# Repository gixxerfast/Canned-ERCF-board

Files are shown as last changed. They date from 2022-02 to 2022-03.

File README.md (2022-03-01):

# Canned-ERCF-board v1.0-beta2
Enraged Rabbit Carrot Feeder CAN-FD expansion board for Duet3

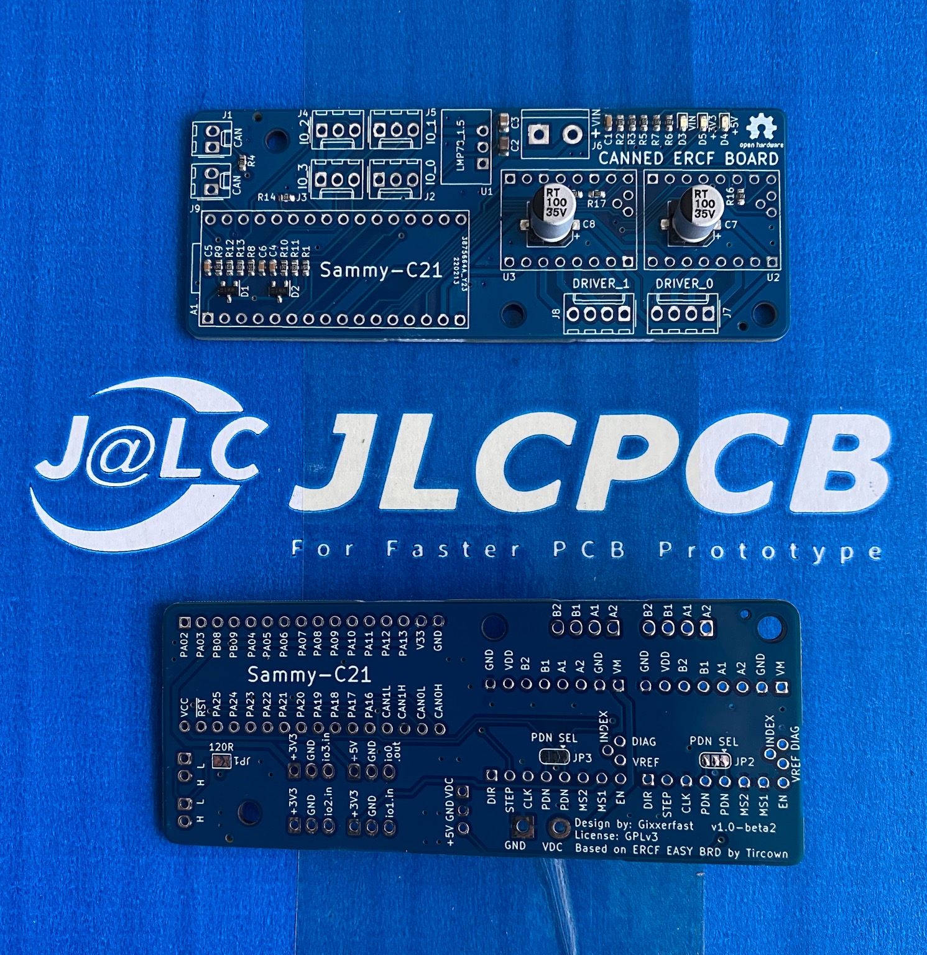
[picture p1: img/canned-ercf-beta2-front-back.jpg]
Canned ERCF boards V1.0-beta2 front and back from JLCPCB


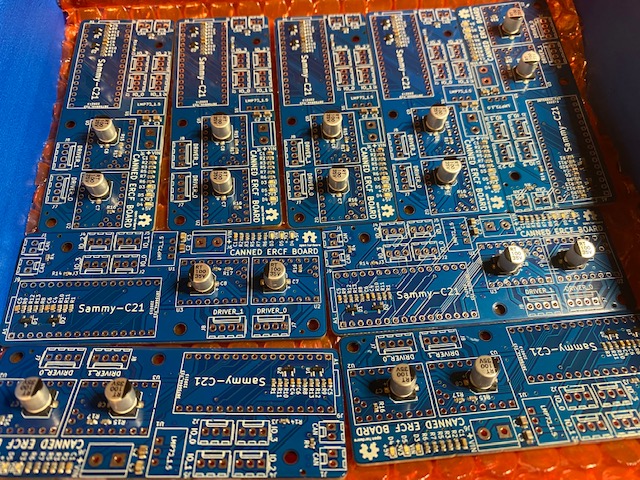
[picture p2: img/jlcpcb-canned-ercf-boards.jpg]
Canned ERCF Boards V1.0-beta2 from JLCPCB


The Canned ERCF board is a general purpose Duet 3 CAN extansion board but specifically made to support the [ERCF](https://github.com/EtteGit/EnragedRabbitProject) multifilament feeder system based on the [ERCF Easy Brd](https://github.com/Tircown/ERCF-easy-brd) by Tircown.

Check out the [Duet RRF ERCF macros](https://github.com/pfn/EnragedRabbitOnRRF?ref=https://coder.social) by pfn. With these macros you should be able to use a RRF equipped printer and run multi filament prints as with the original ERCF macros as long as you have enough ports and motors available.

The board uses a Atmel/Microchip SAM C21 microcontroller module with USB and CAN, the [Sammy-C21](https://www.chip45.com/products/sammy-c21-1.0_atmel_smart_arm_sam_module_samc21_usb_dual_can_duet3d.php) from [Chip45](https://www.chip45.com/).

The firmware is a modified version of the [Duet3Expansion Sammy-C21 firmware](https://github.com/Duet3D/Duet3Expansion) by [Duet3D](https://www.duet3d.com/)  

You can find the fork of the modfied Duet firmware [here](https://github.com/gixxerfast/Duet3Expansion/tree/cannedboard). As the versions are moving rapidly with the new RRF version 3.4 there's no guarantees that this will be kept in synch.

**Please note that this board will not work with the standard Duet Sammy firmware.**

The board features the following functions:

- Support for up to two TMC2209 stepsticks Stepper motor drivers with UART control
- 1500 mA 24V-5V efficient switching voltage regulator. 
- Three GPIO inputs 3.3V signal inputs that may be used for encoders and endstops with 3.3V source.
- One 3.3V PWM output for hobby micro servo control with 5V source. Note that the general advice is not to source power to the servo via the board but to have a separate 5V source.
- MCU Module. It's using the Atmel/Microchip ATSAMC21G18A based Sammy-C21 MCU-module
- Input over voltage protection up to 30V
- VIN voltage monitoring.
- Three led indicators for 3.3V, 5V and VIN (24V). Easy troubleshooting if missing a rail. 

As an extension this board has CAN-FD support and is connected to another Duet 3 board via the CAN bus. Firmware is updated via CAN and the DWC (Duet Web Control frontend) so the USB-port is not really used.

This board can be used with the Sammy-C21 Duet 3 extension board firmware together with my modified configuration file. No further modifications are required (to this date).

There's a 4.7 Kohms pullup resistor on the TX/RX UART line as the BTT TMC2209 stepsticks has a 20K ohms pulldown resistor on the same line. The Duet firmware will disable the UART line before reading and writing causing the the line to go low and therefore corrupt the UART messaging. With the 4.7 Kohms pullup resistor the line is kept high all the time and the communication can function undisturbed.

There are two pin pairs for the CAN bus so either the CAN-bus can be terminated by closing the solder brideg on the back of the board or it can be routed to the next board in the chain,

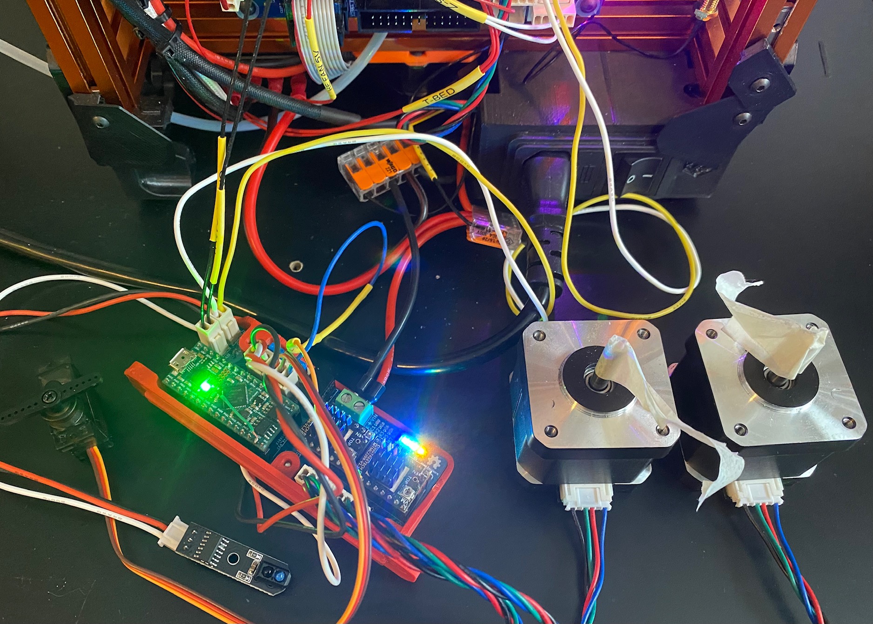
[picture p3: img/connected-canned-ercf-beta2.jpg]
Canned ERCF Board connected to Voron V0.1 Duet 3 mini5+ via CAN


## BOM
Apart from the board as specified in the KiCad files with the SMT components which I have had mounted by JLCPCB, there a number of components needed to complete the board

- 1 x Sammy-C21 ATSAMC21G18A MCU module from [Chip45](https://www.chip45.com/) or [Filastruder](https://www.filastruder.com/products/sammy-c21-v1-0-duet3d-module)
- 2 x BTT TMC2209 stepstick modules
- 1 x LMP78_05-1.5 or compatible DC-DC voltage converter
- 2 x 16 pin PCB connection headers
- 4 x 8 pin PCB connection headers
- 2 x 2 pin PCB connection headers
- 2 x 2 pin MOLEX KK254 (or equivalent) male PCB connectors
- 4 x 3 pin Molex KK254 (or equivalent) male PCB connectors
- 2 x 4 pin Molex KK254 (or equivalent) male PCB connectors
- 1 x 2 pin Phoenix 5.08 Screw connector. Part # 277-1247-ND or eqivalent

### Disclaimer 
This is work in progress and it's right now under development and there may exist issues with this version that may or may not be corrected in the next version. It's based on many parts over which I have no control over at all. I take no responsibilty whatsoever for the functionality or safety and I claim the right to not inform about anything about this product known to me now or in the future. This is soley at your own risk and I accept no responsiblity, financially or otherwise, if it causes your controller board to break, your house to burn down, your wife to divorce you, if it simply doesn't work at all or any other scenario possible in any multiverse. If you do not accept that all responibility for use of this product is your own, please don't download, build or use it.

## License - Open hardware / Open software
This project and its content is realeased under the [GPLv3 license](https://www.gnu.org/licenses/gpl-3.0.html)

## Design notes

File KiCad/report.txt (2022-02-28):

Plotted to 'C:\Users\gixxe\repos\Canned-ERCF-board\KiCad\gerber\canned-ercf-board-F_Cu.gtl'.
Plotted to 'C:\Users\gixxe\repos\Canned-ERCF-board\KiCad\gerber\canned-ercf-board-B_Cu.gbl'.
Plotted to 'C:\Users\gixxe\repos\Canned-ERCF-board\KiCad\gerber\canned-ercf-board-F_Paste.gtp'.
Plotted to 'C:\Users\gixxe\repos\Canned-ERCF-board\KiCad\gerber\canned-ercf-board-F_Silkscreen.gto'.
Plotted to 'C:\Users\gixxe\repos\Canned-ERCF-board\KiCad\gerber\canned-ercf-board-B_Silkscreen.gbo'.
Plotted to 'C:\Users\gixxe\repos\Canned-ERCF-board\KiCad\gerber\canned-ercf-board-F_Mask.gts'.
Plotted to 'C:\Users\gixxe\repos\Canned-ERCF-board\KiCad\gerber\canned-ercf-board-B_Mask.gbs'.
Plotted to 'C:\Users\gixxe\repos\Canned-ERCF-board\KiCad\gerber\canned-ercf-board-Edge_Cuts.gm1'.
Info: Done.

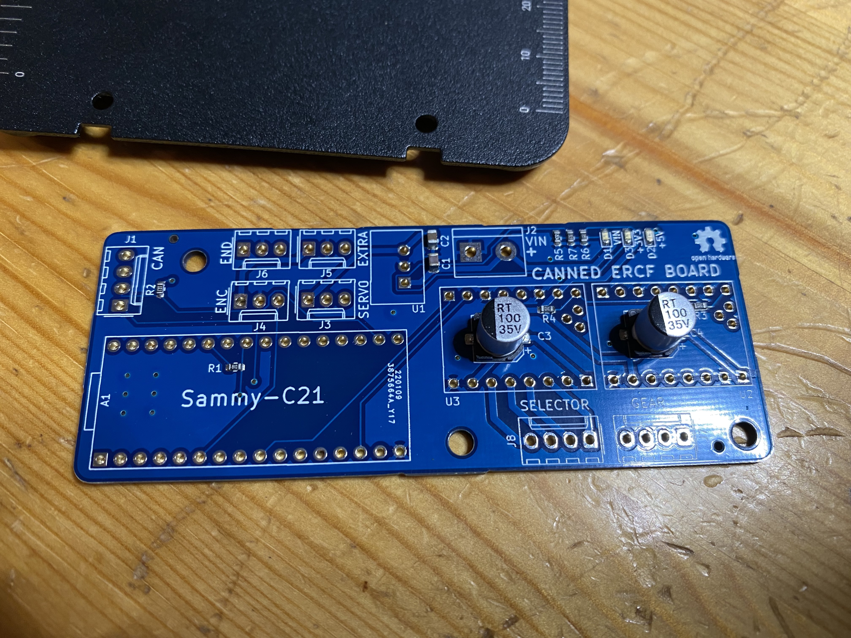
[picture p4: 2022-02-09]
img/canned-ercf-board-front.jpg

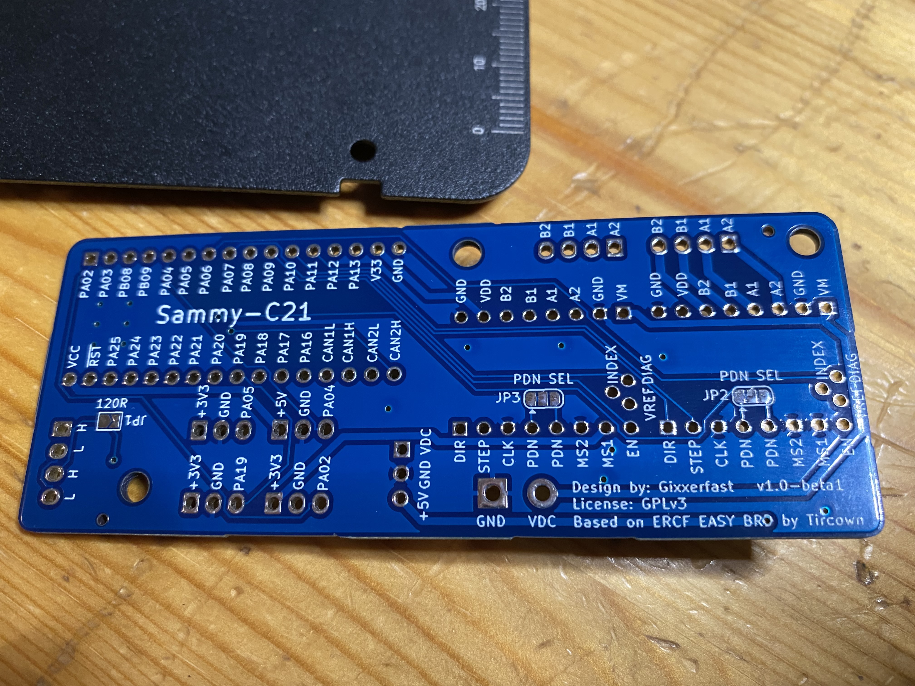
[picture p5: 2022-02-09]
img/canned-ercf-board-rear.jpg

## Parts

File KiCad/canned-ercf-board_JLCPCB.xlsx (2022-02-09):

Comment | Designator | Footprint | JLCPCB Part #（optional）
10uF | C1 | Capacitor_SMD:C_0805_2012Metric |  | C342723
22uF | C2 | Capacitor_SMD:C_0805_2012Metric |  | C338080
100uF | C3, C4 | Capacitor_SMD:CP_Elec_6.3x7.7 |  | C267470
Blue | D1, D2, D3 | LED_SMD:LED_0603_1608Metric |  | C138541
1k | R1, R6 | Resistor_SMD:R_0603_1608Metric |  | C116692
120R | R2 | Resistor_SMD:R_0603_1608Metric |  | C365072
10k | R3, R4 | Resistor_SMD:R_0603_1608Metric |  | C98220
4K7 | R5 | Resistor_SMD:R_0603_1608Metric |  | C99782
470R | R7 | Resistor_SMD:R_0603_1608Metric |  | C114669

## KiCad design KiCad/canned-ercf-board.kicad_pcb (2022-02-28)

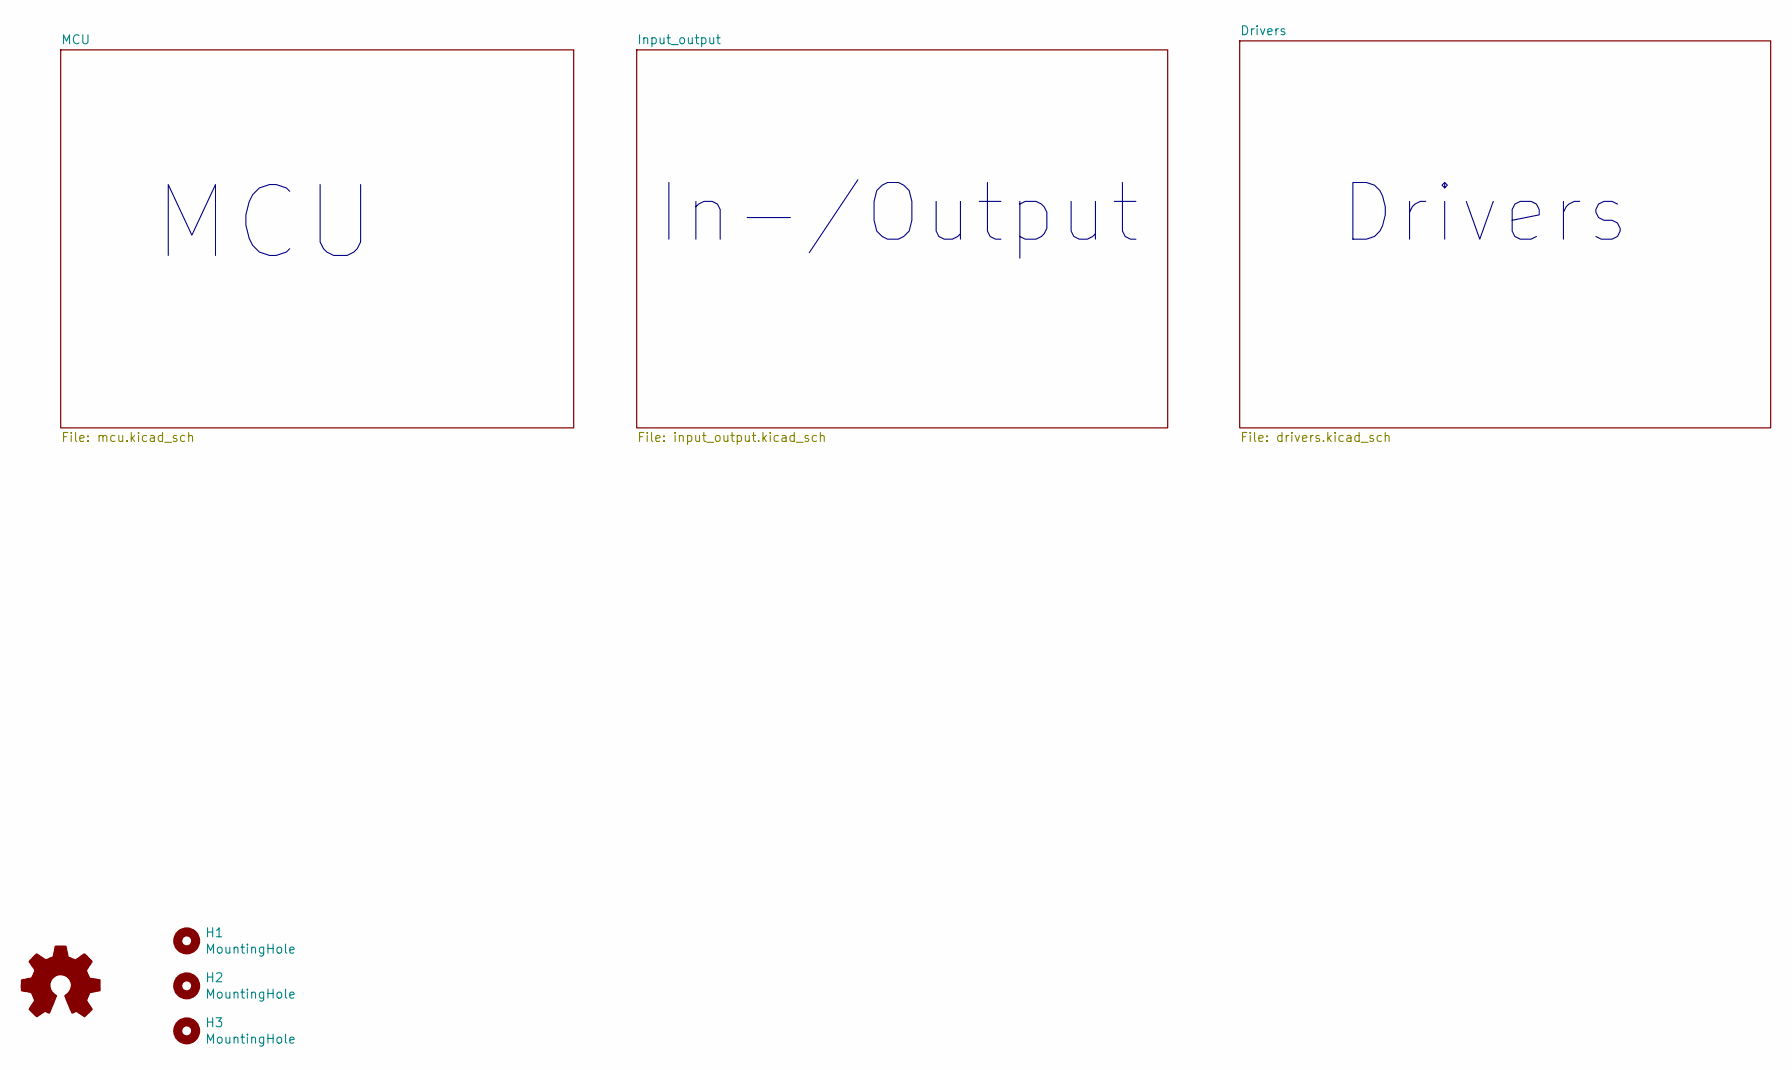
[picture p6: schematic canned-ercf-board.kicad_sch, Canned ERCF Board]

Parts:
H1, H2, H3: MountingHole; MountingHole_3.2mm_M3
L1: Logo_Open_Hardware_Small; OSHW-Logo2_7.3x6mm_SilkScreen

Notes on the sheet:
MCU
Drivers
In-/Output

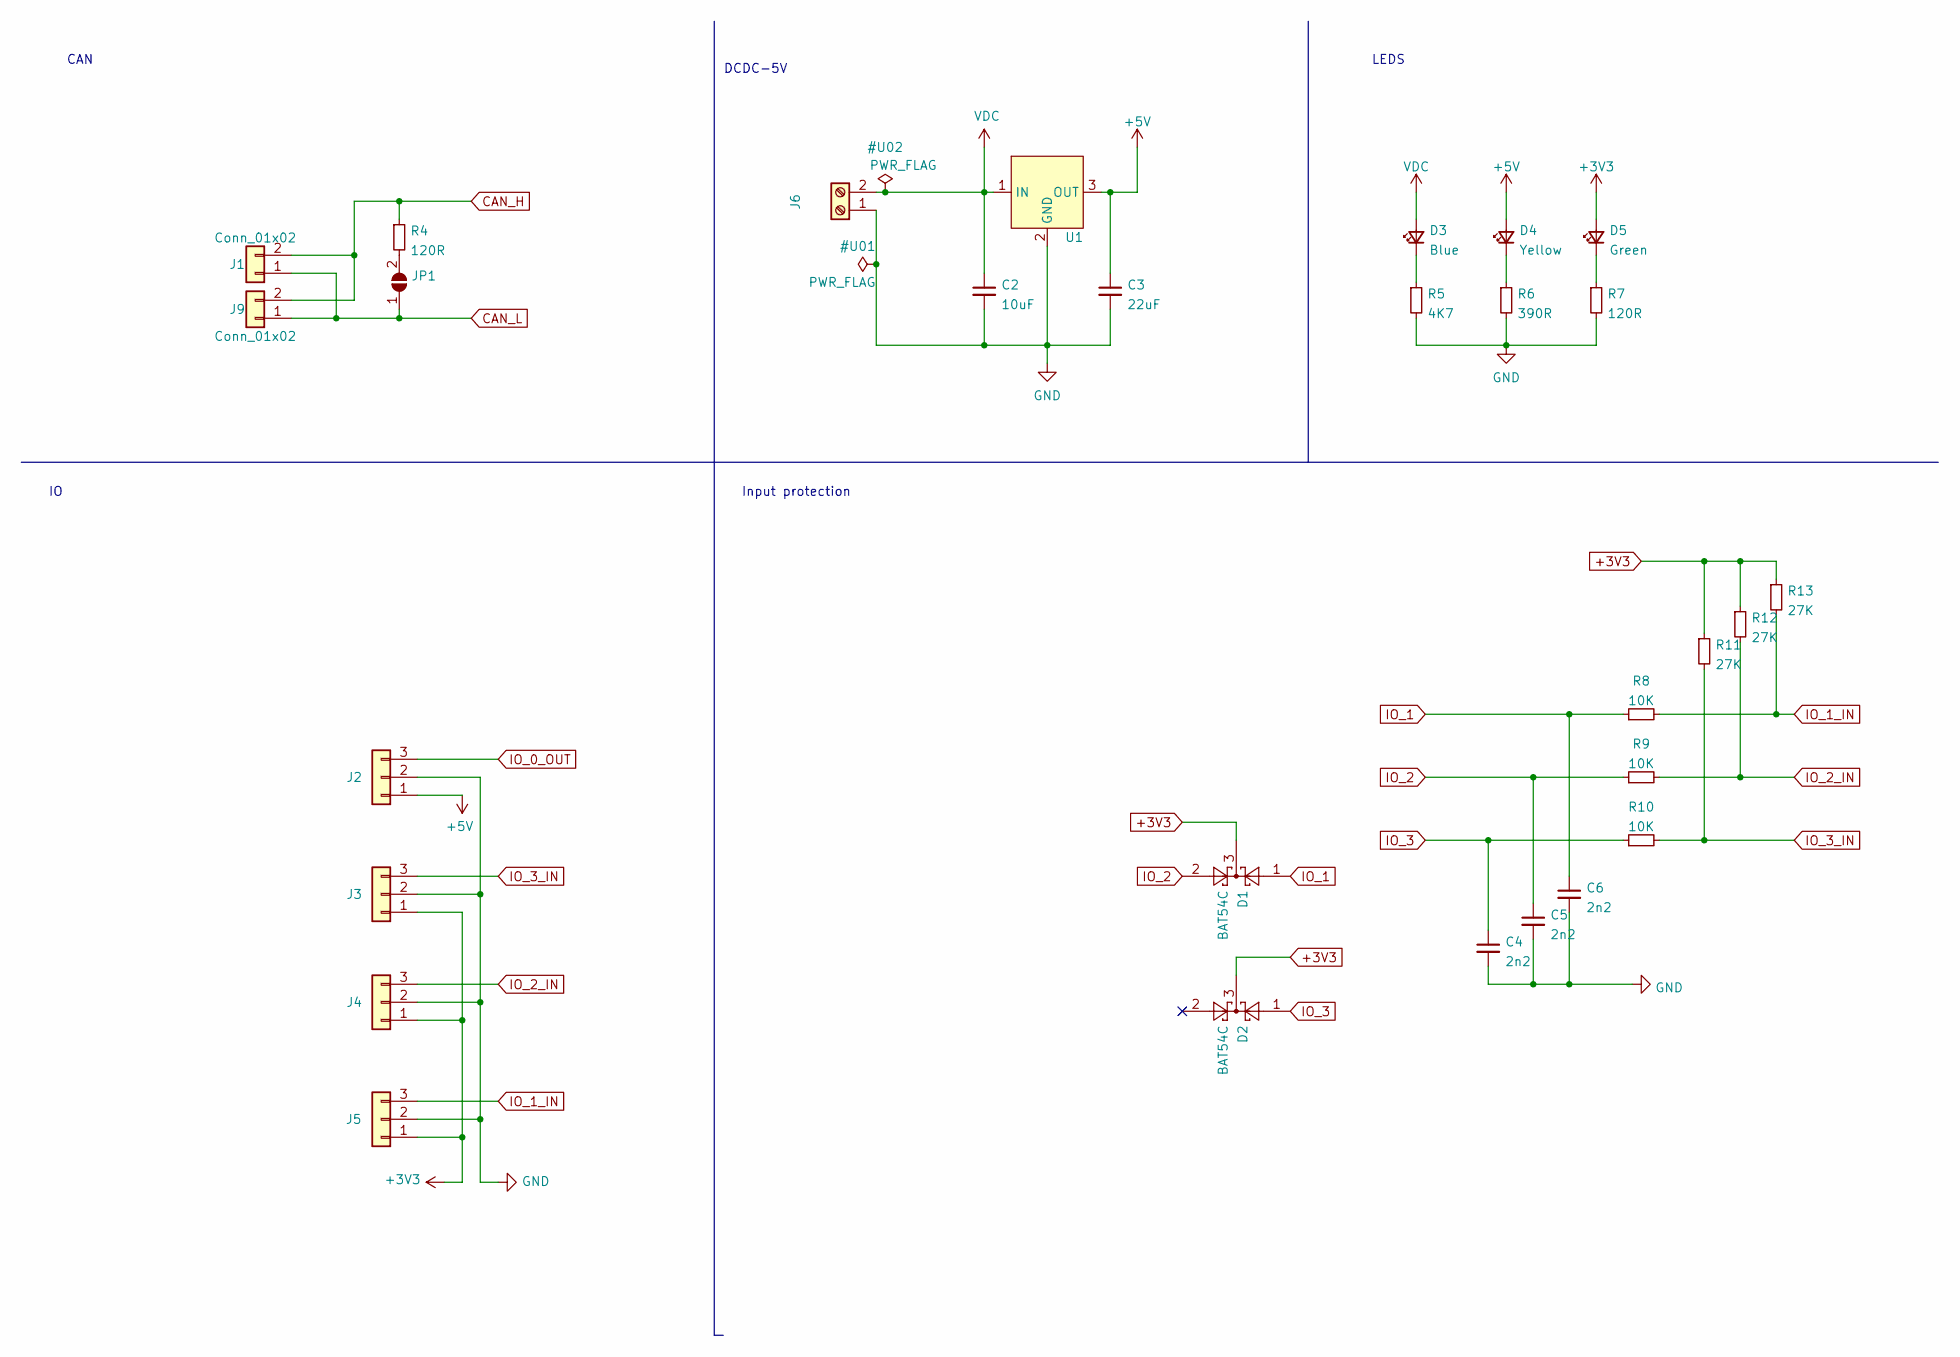
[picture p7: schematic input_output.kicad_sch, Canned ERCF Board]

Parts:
C2: 10uF; C_0805_2012Metric; Part GRM21BR61H106KE43L; LCSC C440198
C3: 22uF; C_0805_2012Metric; Part CL21A226MAQNNNE; LCSC C45783
C4, C5, C6: 2n2; C_0603_1608Metric; Part 0603B222K500NT; LCSC C1604
D1, D2: BAT54C; SOT-23; Part BAT54C,215; LCSC C37704
D3: Blue; LED_0603_1608Metric; Part 19-217/BHC-ZL1M2RY/3T; LCSC C72041
D4: Yellow; LED_0603_1608Metric; Part 19-213/Y2C-CQ2R2L/3T(CY); LCSC C72038
D5: Green; LED_0603_1608Metric; Part 19-217/GHC-YR1S2/3T; LCSC C72043
J1, J9: Conn_01x02; Molex_KK-254_AE-6410-02A_1x02_P2.54mm_Vertical
J2, J3, J4, J5: Conn_01x03_Male; Molex_KK-254_AE-6410-03A_1x03_P2.54mm_Vertical
J6: Screw_Terminal_01x02; TerminalBlock_bornier-2_P5.08mm_2; Part 1729128; LCSC C91153
JP1: SolderJumper_2_Open; SolderJumper-2_P1.3mm_Open_TrianglePad1.0x1.5mm
R4, R7: 120R; R_0603_1608Metric; Part 0603WAF1200T5E; LCSC C22787
R5: 4K7; R_0603_1608Metric; Part 0603WAF4701T5E; LCSC C23162
R6: 390R; R_0603_1608Metric; Part 0603WAF3900T5E; LCSC C23151
R8, R9, R10: 10K; R_0603_1608Metric; Part 0603WAF1002T5E; LCSC C25804
R11, R12, R13: 27K; R_0603_1608Metric; Part 0603WAF2702T5E; LCSC C22967
U1: Switching_Regulator_LMP78_05-1.5; Switching_regulator_POL_LMP78_1.5

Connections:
+5V: C3.1, D4.2 (A), J2.1, U1.3 (OUT); also elsewhere on the board
CAN_H: J1.2, J9.2, R4.1; also elsewhere on the board
CAN_L: J1.1, J9.1, JP1.1 (A); also elsewhere on the board
IO_0_OUT: J2.3; also elsewhere on the board
IO_1: C6.1, D1.1, R8.1; also elsewhere on the board
IO_1_IN: J5.3, R8.2, R13.2
IO_2: C5.1, D1.2, R9.1; also elsewhere on the board
IO_2_IN: J4.3, R9.2, R12.2
IO_3: C4.1, D2.1, R10.1; also elsewhere on the board
IO_3_IN: J3.3, R10.2, R11.2
unnamed: D3.1 (K), R5.1
unnamed: D4.1 (K), R6.1
unnamed: D5.1 (K), R7.1
unnamed: JP1.2 (B), R4.2

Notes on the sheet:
CAN
Input protection
LEDS
DCDC-5V

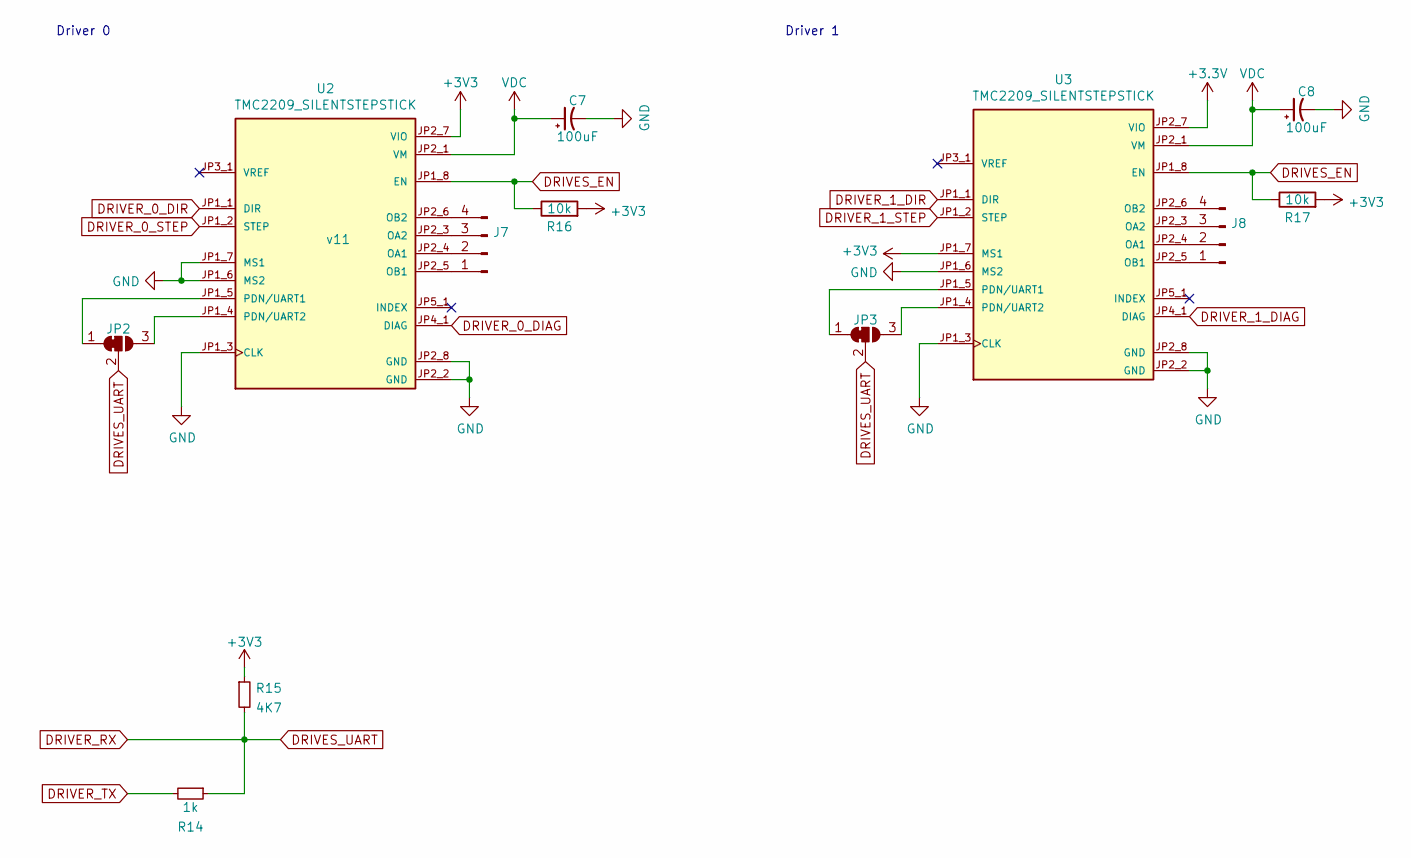
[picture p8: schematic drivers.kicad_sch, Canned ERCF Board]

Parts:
C7, C8: 100uF; CP_Elec_6.3x7.7; Part RT1V101M0607; LCSC C267470
J7, J8: Conn_01x04_Male; Molex_KK-254_AE-6410-04A_1x04_P2.54mm_Vertical
JP2, JP3: SolderJumper_3_Bridged12; SolderJumper-3_P1.3mm_Bridged12_RoundedPad1.0x1.5mm
R14: 1k; R_0603_1608Metric; Part 0603WAF1001T5E; LCSC C21190
R15: 4K7; R_0603_1608Metric; Part 0603WAF4702T5E; LCSC C23162
R16, R17: 10k; R_0603_1608Metric; Part 0603WAF1002T5E; LCSC C25804
U2, U3: TMC2209_SILENTSTEPSTICK; MODULE_TMC2209_SILENTSTEPSTICK; PARTREV v11

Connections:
DRIVER_0_DIAG: U2.JP4_1 (DIAG); also elsewhere on the board
DRIVER_0_DIR: U2.JP1_1 (DIR); also elsewhere on the board
DRIVER_0_STEP: U2.JP1_2 (STEP); also elsewhere on the board
DRIVER_1_DIAG: U3.JP4_1 (DIAG); also elsewhere on the board
DRIVER_1_DIR: U3.JP1_1 (DIR); also elsewhere on the board
DRIVER_1_STEP: U3.JP1_2 (STEP); also elsewhere on the board
DRIVER_RX: JP2.2 (C), JP3.2 (C), R14.1, R15.2; also elsewhere on the board
DRIVER_TX: R14.2; also elsewhere on the board
DRIVES_EN: R16.1, R17.1, U2.JP1_8 (EN), U3.JP1_8 (EN); also elsewhere on the board
unnamed: J7.1, U2.JP2_5 (OB1)
unnamed: J7.2, U2.JP2_4 (OA1)
unnamed: J7.3, U2.JP2_3 (OA2)
unnamed: J7.4, U2.JP2_6 (OB2)
unnamed: J8.1, U3.JP2_5 (OB1)
unnamed: J8.2, U3.JP2_4 (OA1)
unnamed: J8.3, U3.JP2_3 (OA2)
unnamed: J8.4, U3.JP2_6 (OB2)
unnamed: JP2.1 (A), U2.JP1_5 (PDN/UART1)
unnamed: JP2.3 (B), U2.JP1_4 (PDN/UART2)
unnamed: JP3.1 (A), U3.JP1_5 (PDN/UART1)
unnamed: JP3.3 (B), U3.JP1_4 (PDN/UART2)

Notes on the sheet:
Driver 1
Driver 0

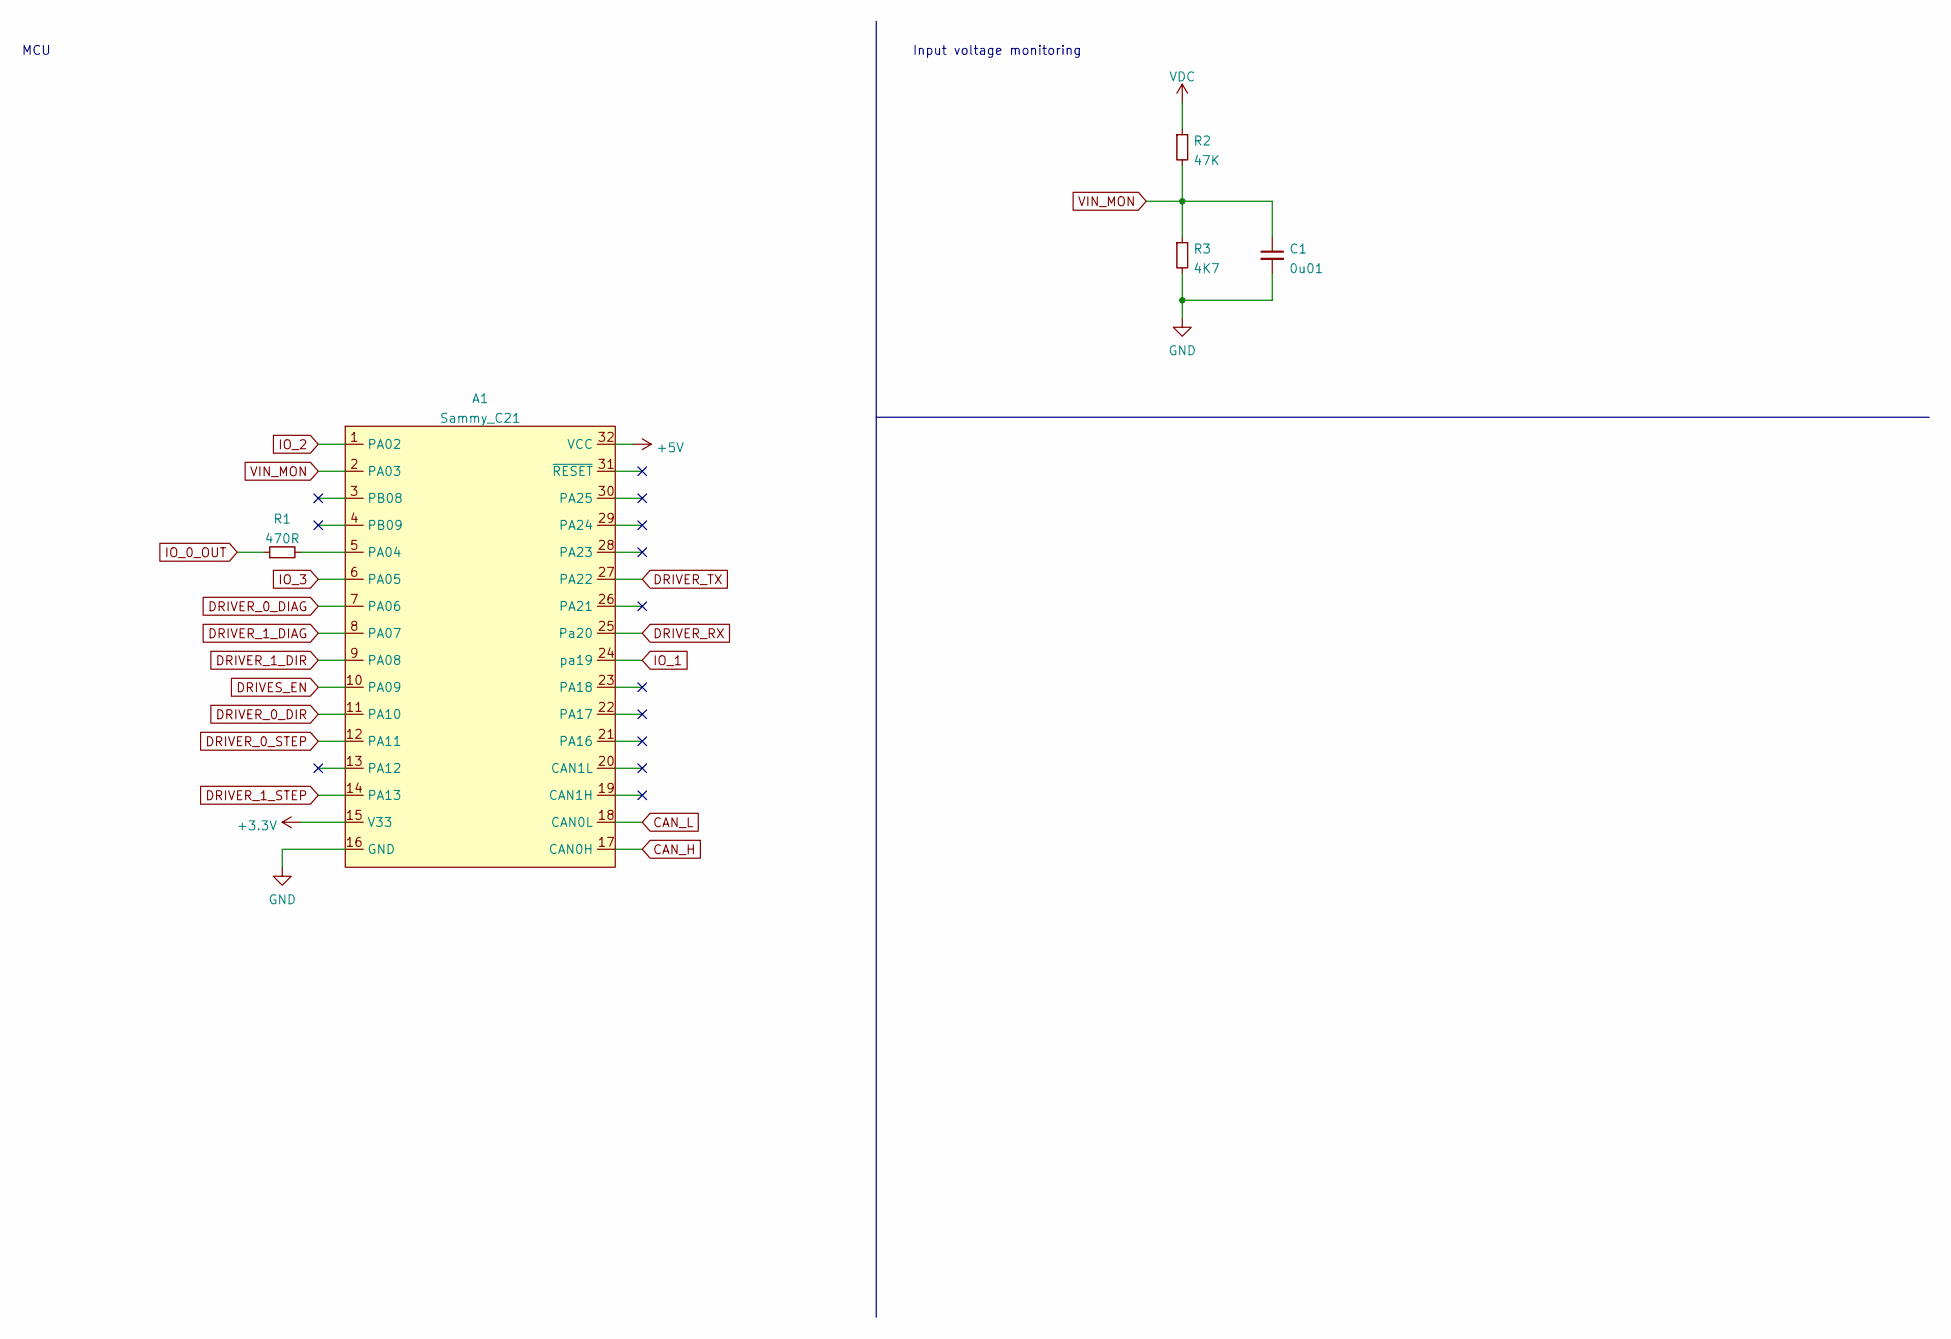
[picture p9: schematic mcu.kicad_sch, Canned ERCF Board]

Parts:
A1: Sammy_C21; Sammy_C21_Module_DIL32_2.54
C1: 0u01; C_0603_1608Metric; Part 0603B103K500NT; LCSC C57112
R1: 470R; R_0603_1608Metric; Part 0603WAF4700T5E; LCSC C23179
R2: 47K; R_0603_1608Metric; Part 0603WAF4702T5E; LCSC C25819
R3: 4K7; R_0603_1608Metric; Part 0603WAF4701T5E; LCSC C23162

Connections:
+5V: A1.32 (VCC); also elsewhere on the board
CAN_H: A1.17 (CAN0H); also elsewhere on the board
CAN_L: A1.18 (CAN0L); also elsewhere on the board
DRIVER_0_DIAG: A1.7 (PA06); also elsewhere on the board
DRIVER_0_DIR: A1.11 (PA10); also elsewhere on the board
DRIVER_0_STEP: A1.12 (PA11); also elsewhere on the board
DRIVER_1_DIAG: A1.8 (PA07); also elsewhere on the board
DRIVER_1_DIR: A1.9 (PA08); also elsewhere on the board
DRIVER_1_STEP: A1.14 (PA13); also elsewhere on the board
DRIVER_RX: A1.25 (Pa20); also elsewhere on the board
DRIVER_TX: A1.27 (PA22); also elsewhere on the board
DRIVES_EN: A1.10 (PA09); also elsewhere on the board
IO_0_OUT: R1.1; also elsewhere on the board
IO_1: A1.24 (pa19); also elsewhere on the board
IO_2: A1.1 (PA02); also elsewhere on the board
IO_3: A1.6 (PA05); also elsewhere on the board
unnamed: A1.5 (PA04), R1.2
VIN_MON: A1.2 (PA03), C1.1, R2.2, R3.1

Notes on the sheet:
Input voltage monitoring
MCU

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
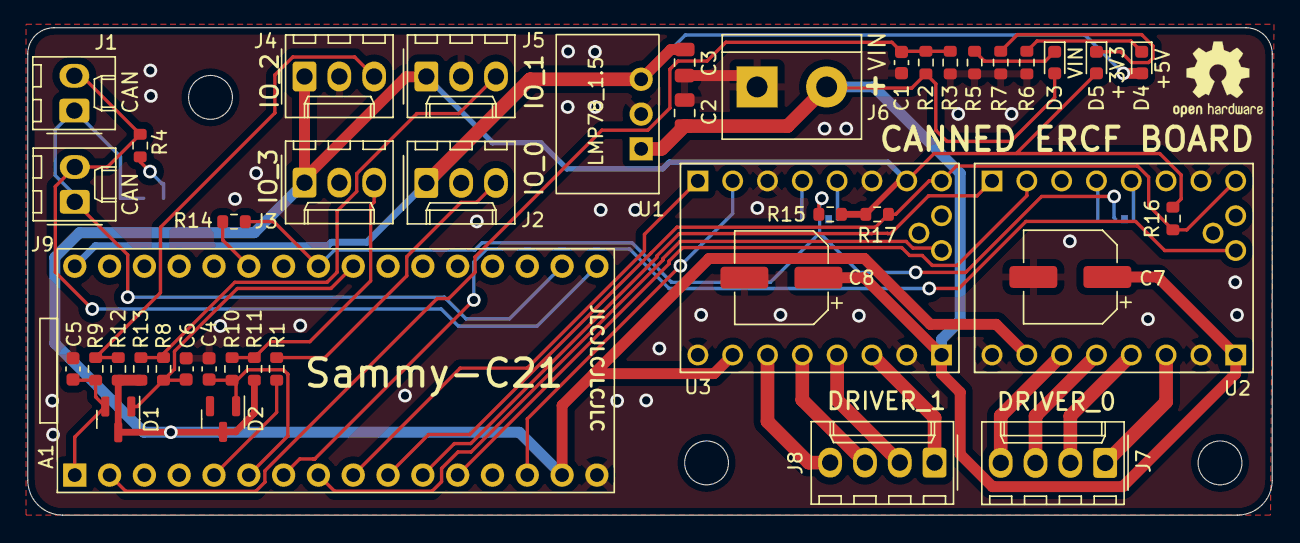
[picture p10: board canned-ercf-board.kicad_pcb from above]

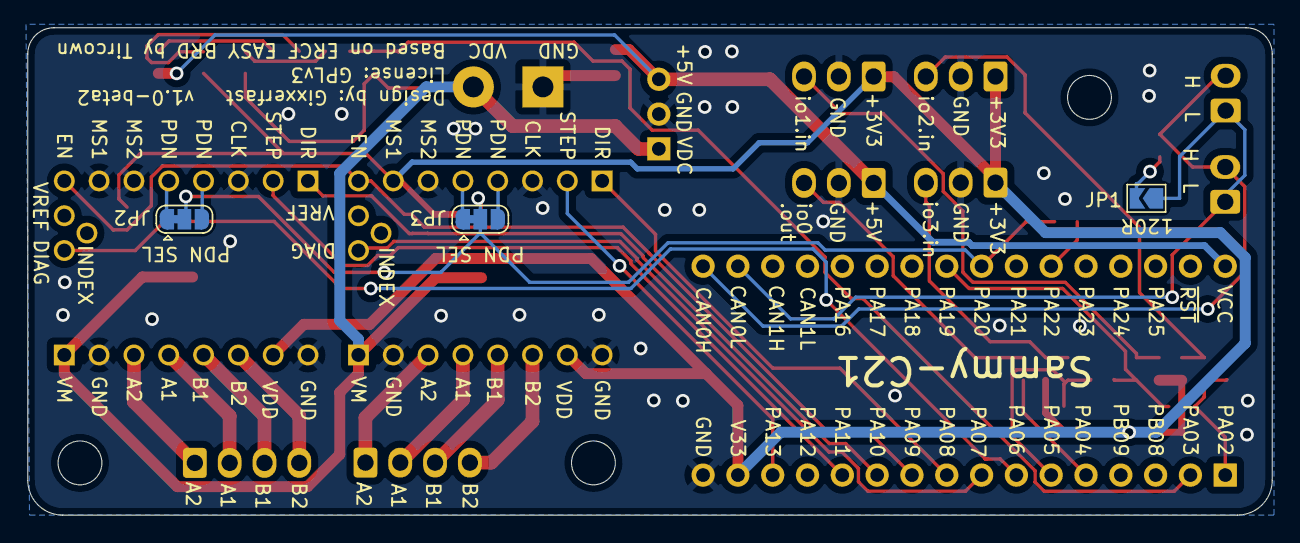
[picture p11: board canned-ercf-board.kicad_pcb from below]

Board: 2 copper layers, 90.8 x 35.6 mm, 50 parts (3 on the bottom side), 40 nets.

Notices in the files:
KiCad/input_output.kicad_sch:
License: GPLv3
